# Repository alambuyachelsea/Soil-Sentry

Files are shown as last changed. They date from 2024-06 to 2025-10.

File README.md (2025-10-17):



## Table of contents
- [Author](#author)
- [Project Overview](#project-overview)
- [Estimated Time](#estimated-time)
- [Project Objective](#project-objective)
- [Bill of Materials](#bill-of-materials)
- [Computer Setup](#computer-setup)
  - [IDE](#ide)
  - [Raspberry Pi Pico W Setup](#raspberry-pi-pico-w-setup)
  - [Wiring](#wiring)
- [Platform for Data Transmission](#platform-for-data-transmission)
- [The Code](#the-code)
  - [Controller Code](#controller-code)
  - [Server Code](#server-code)
- [Final Look](#final-look)

## Author
By Alambuya Chelsea

## Project Overview
The soil sentry is a small scale irrigation system which allows a user to connect multiple plants with various water consumption needs, monitor their water levels and supply water them when needed in addition to monitoring the water reservoir levels. 

## Estimated Time
- Setting up the whole project with the IDE and getting everything connected takes about 5 hours with 2 hours of active setup and about 3 hours for designing a 3D printing the reservoir mount where ultrasonic sensor will rest. The container I chose for the reservoir was relatively small so this the printing did not take much time, see the picture below
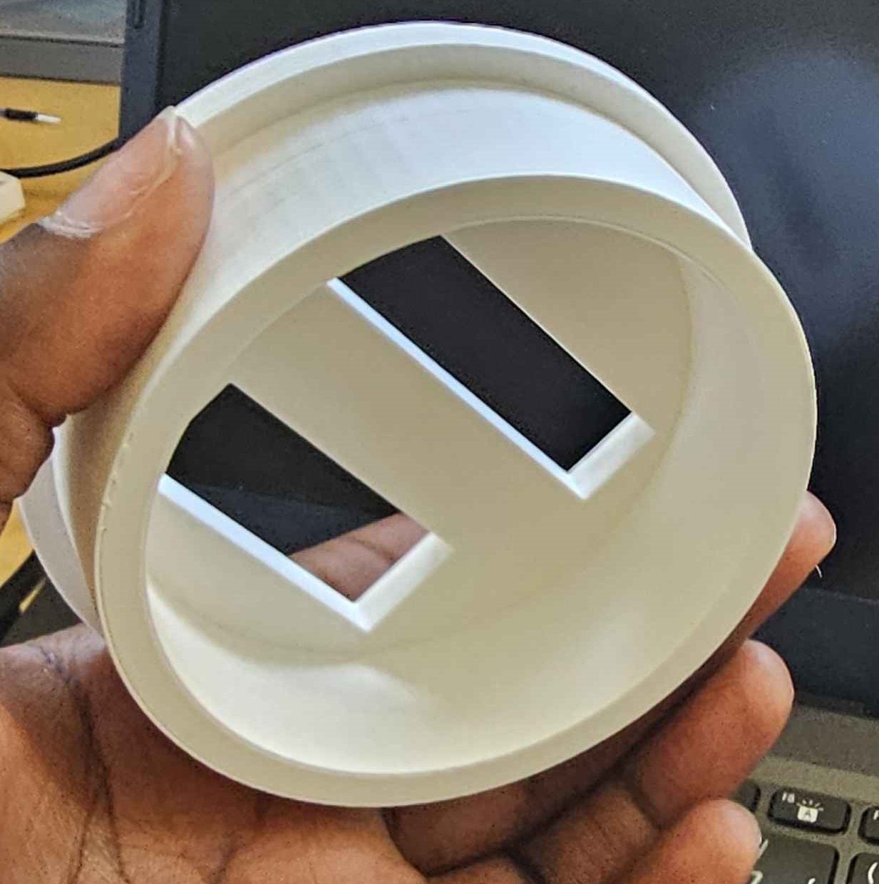
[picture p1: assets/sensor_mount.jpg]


## Project Objective
Many at home watering solutins exist but are limited to just soil moisture levels and water supply. These solutions are sufficient for plants that have the same water consumption needs but to an owner of various plant types like succulents, herbs and flowering plants this can lead to over or under watering plants by trying to calibrate a single water supply to them.
With the soil sentry, a user can create differnt plant profiles where each plant's water consumption needs will determine how offen it recieves water from the supply. Additionally, the water reservoir is monitored which allows the user to know when re-fill it.
By monitoring the data, users can have a better idea of their plant needs, reduce water waste by ensuring the plants are only watered when they need it.

## Bill of Materials
These items can be purchased online at stores that sells electronic components, single board computers, modules, sensors etc. Reliable options are [The pi hut](thepihut.com), [electrokit](electrokit.com), [amazon.se](amazon.se) and any non electronic components can be found at a hardware store.
|Image|Component|Price (SEK)|Purpose|
|---|---|---|-----|
|Raspberry Pi Pico W |Raspberry Pi Pico W| 89| Reads the sensor data and transmits it to the server|
|Soil Moisture Sensor |Capacitive Soil Moisture Sensor V2.0 *| 44| To measure the soil moisture level |
|Submersible waterpump 3V |Submersible waterpump 3V *| 45| To pump the water from the reservoir to the plants|
|5V Relay Module|5V Relay Module *| 60|Handles switching operations between the 3V pump and a separate 5V control signal|
|9V Battery|9V Battery|60|Power Supply for the water  pumps|
|Battery cord|Battery cord|20|Connects battery to power supply module|
|Breadboard Power Supply Module|Breadboard Power Supply Module|60|Power Supply to the breadboard for the water  pumps|
|HC-SR04 Ultrasonic Range Sensor|HC-SR04 Ultrasonic Range Sensor| 23| To measure the reservoir level|
|Male-Male Jumper Wires|Male-Male Jumper Wires| 100| To connect components to the Pico|
|Female-Male Jumper Wires|Female-Male Jumper Wires| 100| To connect components to the Pico|
|Female-Female Jumper Wires|Female-Female Jumper Wires| 100| To connect components to the Pico|
|Silicon Water Pipe|Silicon Water Pipe| 45| To transport water to the plant|
|2 Core Electric Cable|2 Core Electric Cable| 121| To extend the length of jumper wires|
|Soldering Iron Kit|Soldering Iron Kit| 500| To join 2 wires|
|Solder Wire|Solder Wire| 100| To join 2 wires|
|Desoldering Wick|Desoldering Wick| 100| To erase the makes you made (with the soldering, not in real life)|
|Electric Tape|Electric Tape| 60| To seal soldered wires that will be placed in water|
|Heat Shrink|Heat Shrink| 90| To seal soldered wires that will be placed in water|

  * Get one per plant you intend to monitor

## Computer Setup
### IDE
I developed this on a computer running windows 11. I decided to use Thonny for the microcontroller code because it is specifically designed for beginners in MicroPython programming, offering an intuitive interface, easy debugging tools for microcontroller projects. Installation instruction can be found on the [Thonny website](https://thonny.org/). For the server side code I used VS Code which you can download and install on the [Visual Studio Code website](https://code.visualstudio.com/download)

### Raspberry Pi Pico W setup
To set up the pico first download the latest version of Raspberry Pi Pico W firmware [here](https://rpf.io/pico-w-firmware), once downloaded connect the pico to your computer while holding down the bootsel button. A file manager should open with the raspberry pi pico w as the connected device, copy the firmware file to the device and the file manager will close. Open the Thonny editor and on the navigation bar, select Tools > Options > Interpreter and choose the MicroPython interpreter for Raspberry Pi Pico.

### Wiring
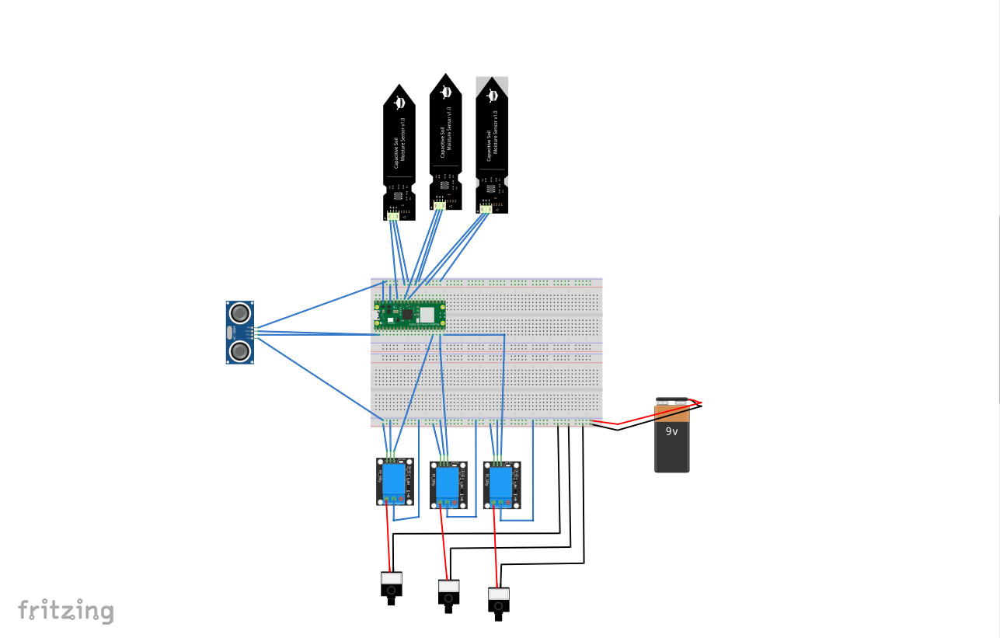
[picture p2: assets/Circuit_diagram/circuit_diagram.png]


- Breadboard - I connected 2 boards to reduce crowding but it's possible to have everything on one.

- Raspberry Pi Pico W - place the Pico over the center of the breadboard with the pins straddling the center divide. Connect the pico's GND to the (-) line on the right side of the breadboard and the 3V3 output to the (+) line on the on the right side of the breadboard. See the attached pico w pinout for guidance. 
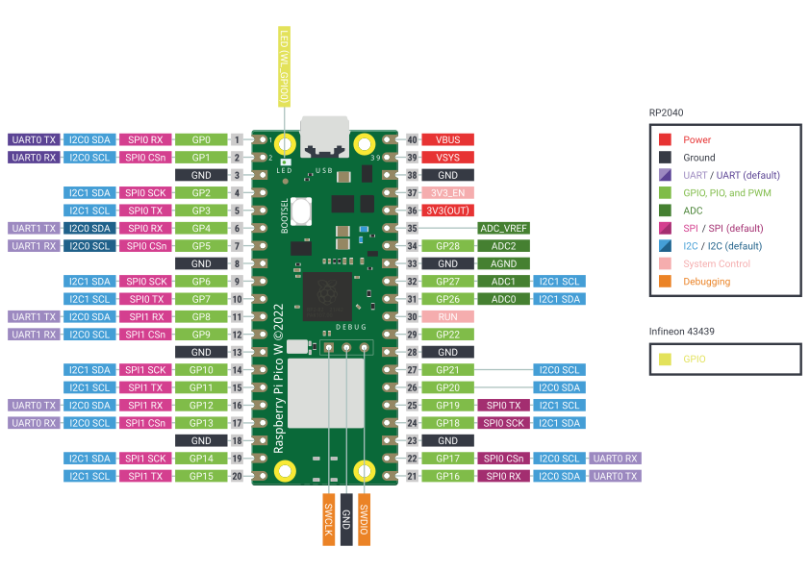
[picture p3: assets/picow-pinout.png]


- Power Supply module and 9V Battery - Connect the battery to the power supply module using the battery cord. Connect the power supply's GND pin to the left side (-) line and the 5V pin to the left side (+) line, turn on the power supply by pressing the power button.

- Soil moisture sensors - For my set up, I used analog sensors so I was limited to 3 analog to digital converter (ADC) pins on the pico i.e. GP26, GP27 and GP28. This will be placed in the soil to measure the moisture content. Connect the sensor's vcc to the (+) line on the bread board, the GND to the (-) line on the breadboard and the analog output to one of the ADC pins. Since soil sensors are different you may have to calibrate them according to your environment. Follow these steps to calibrate them;

  - Take readings in open air, very dry soil, dry soil, lightly watered soil, heavily watered soil and 100% water. 
  - Take about 100 readings for each  and find the highest and lowest values
  - Create a scale of 0 - 5 where 0 is open air and 5 is 100% water.

- Ultra sonic sensor - This should rest on top of the water reservoir. For this project, I designed a 3D mount to set on top of the reservoir. Connect the sensor's GND to any (-)line on the breadboard and the vcc to any (+) line on the breadboard. Connect the trig pin to GPIO 0 and connect the echo pin to GPIO 1.
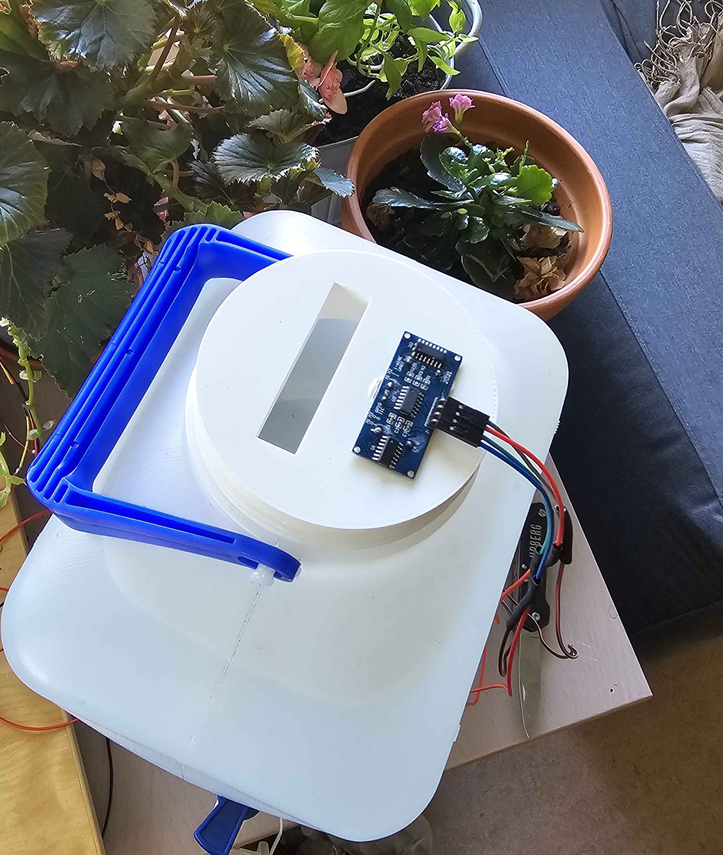
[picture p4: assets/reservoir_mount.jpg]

Calibrating the ultra sonic sensor is similar to the soil moisture sensors;
  - Set up the sensor above the reservoir and take readings when the reservoir is empty, and slowly increase the water level taking several readings as you go.
  - Create a percentage scale after getting the reading at multiple levels.

- Water Pump and 5V relay module - Connect the water pump's gnd to the left side (-) line on the breadboard and the the pump's (+) line to the relays normally open(NO) terminal. Then connect the relay's (-) and (+) pins to the GND and the (+) line on the left side of the breadboard. Connect the relays control input pin to any available GPIO pin.

### Platform for Data Transimission
- For the project, I decided to send the sensor data via a json data file sent over HTTP. I set up a server on my laptop to listen for data transmitted by the pico inorder to process it. 
- When the pico connects to the same network as the server, the sensor data is read and transmitted to the server as a POST request and stored as a variable. 
- When the dashboard is requested for from a browser, the server servers the index.html file (styled with css) and JavaScript method requests for the data to be displayed. 
- At this point, the data has been recieved by the server and stored in a variable so this information is sent. I decided to create a custom dashboard as I felt the available options were too restricting in how the data could be visualized and additionally I could style it to my preference.

### The Code
#### Controller Code
The code is fairly straight forward. In controller_code folder is the code to be uploaded to the Raspberry Pi Pico W and works as follows,
  - plant_profile.py: This class allows different plant types to be created with specific water needs, a soil sensor pin and a water pump pin.
  - water_pump.py: This allows the water to be turned on and off when a plant requires water
  - Soil_sensor.py: This takes the soil moisture level and converts it according to the scale created during the sensor calibration
  - ultrasonic_sensor.py: This transimits a sonic pulse, waits for an encho and uses the time difference to determine how far the water is from the sensor, this is then converted to an approximate percentage of remaining water in the reservoir.
  - main.py: This is where different plant profiles are created with their respective soil sensors and water pump pins. The ultra sonic sensor is also initialized with the trigger and echo pins. The program then periodically reads data from the various sensors and transmits it to the server via an HTTP POST request. After the data is transmitted, the reservoir level is checked to make sure there's enough enough water to water  the plants, if there is, all the plants' current water levels are checked to see if they fall below their water needs. If the water level is below their needs, then it's associated pump is turned on for 10 seconds which provides sufficient water to increase it's current water level and then turned off. After one hour, the process is repeated.

#### Server code
This Python script sets up a system to manage sensor data through both an HTTP server and a WebSocket server. The HTTP server, built using `BaseHTTPRequestHandler` and `HTTPServer`, handles GET requests to serve static files like `index.html`, `styles.css`, and `script.js`, as well as JSON data for endpoints such as `/plants` and `/ultrasonic_reading`. It also handles POST requests to receive sensor data at the `/receive_data` endpoint, storing this data in a global dictionary `sensor_data`. When new sensor data is posted, it is also sent to all connected WebSocket clients using asynchronous communication.

The WebSocket server, created with the `websockets` library, manages real-time communication with clients. It handles incoming WebSocket connections and responds to requests for sensor data. A function `send_data_to_clients` is used to broadcast updated sensor data to all connected WebSocket clients. Both servers are run concurrently: the HTTP server in a separate thread and the WebSocket server in the main thread, allowing the system to handle HTTP requests and WebSocket communication simultaneously. This setup facilitates a dashboard webpage where clients can receive dynamic updates of sensor data in real-time.

## Data Visualization
The dasboard can be deívided into 3 main parts
- The Reservoir. This shows the reservoirs approximate level after readings are taken and converted to a percentage.
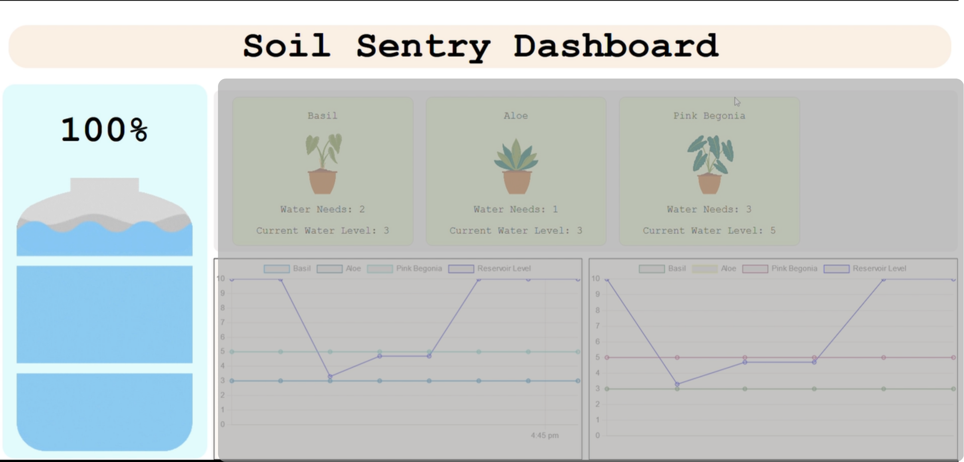
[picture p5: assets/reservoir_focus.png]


- Plant section. Here the user can view all the plants currently being monitored, their name, current water level (which is updated every hour) and water needs
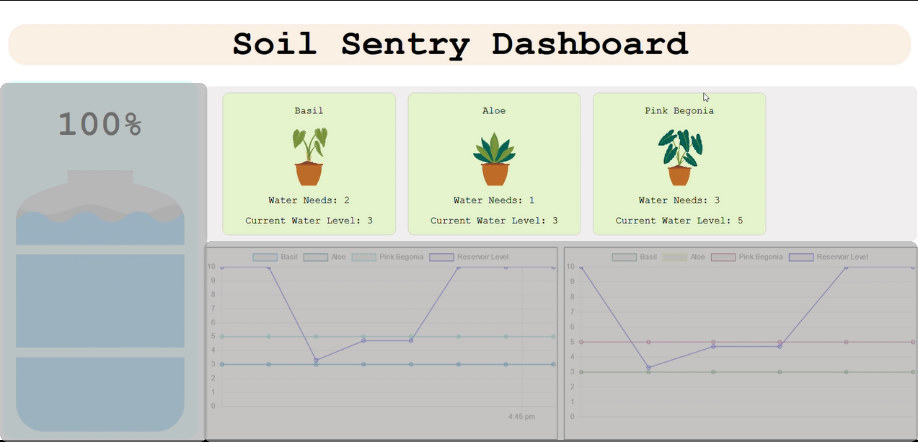
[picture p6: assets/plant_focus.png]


- Graph section. This further split into:
  - Hourly section. This shows the plants current water level as the rservoir level and this is recorded every hour of the day.
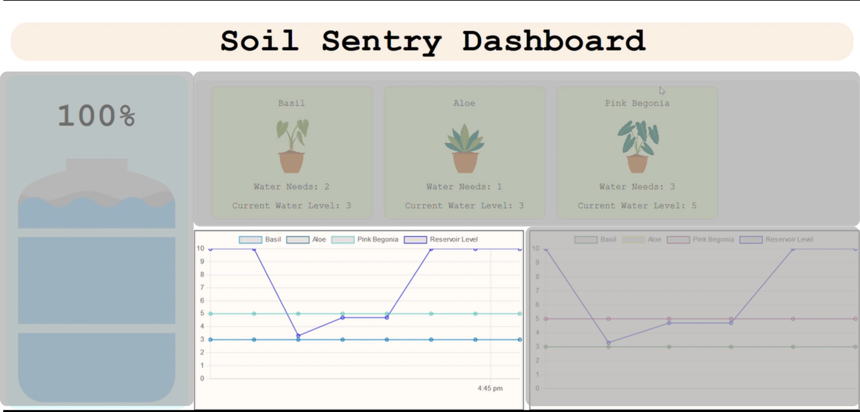
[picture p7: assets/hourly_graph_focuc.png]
  

  - Weekly section. This shows that plants average water level for the last 24 hours
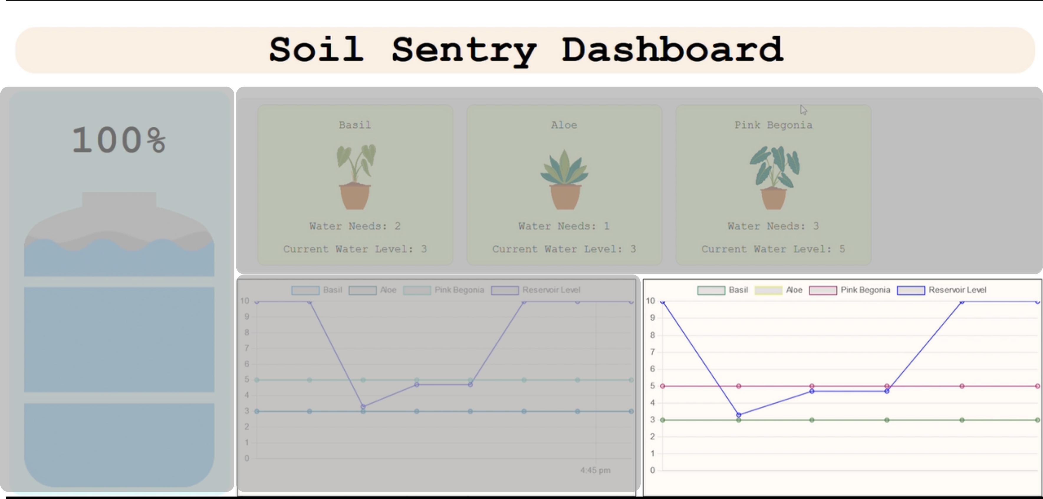
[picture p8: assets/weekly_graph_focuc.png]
  

## Final look
Over all, the roject turned out as I origianlly designed but throught out the process I realized I was limited to only 3 three ADC pins on the pico so if i wanted to add more plants I'd have to purchase an additional digital soils sensor. It was also quite difficult to calibrate the soil sensors as they were quite immprecise and had verry different ranges.

The final dashboard
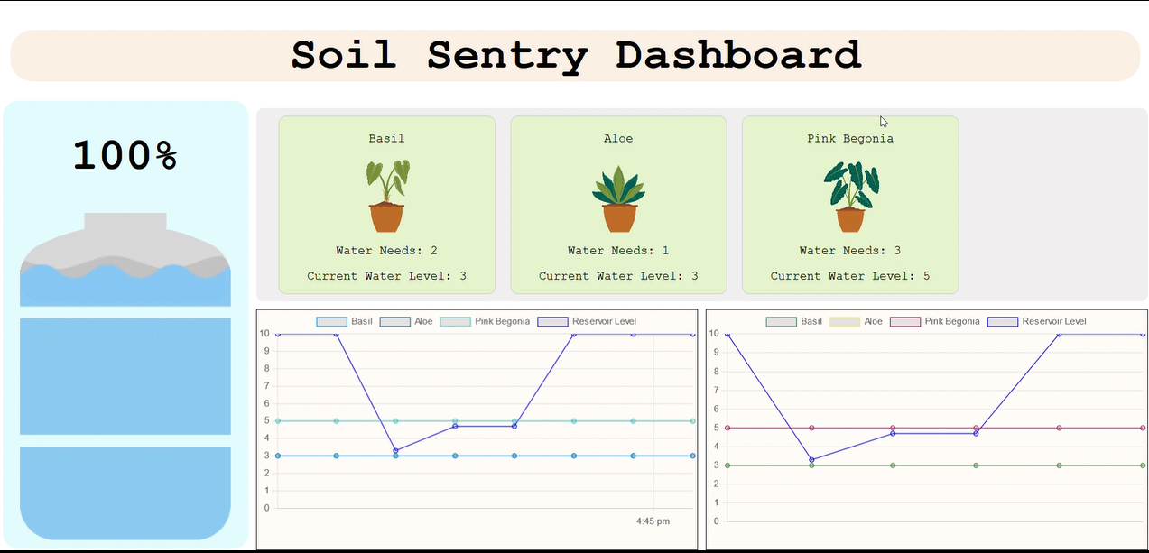
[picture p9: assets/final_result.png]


Plant window with multiple plants



Final Setup shot 1
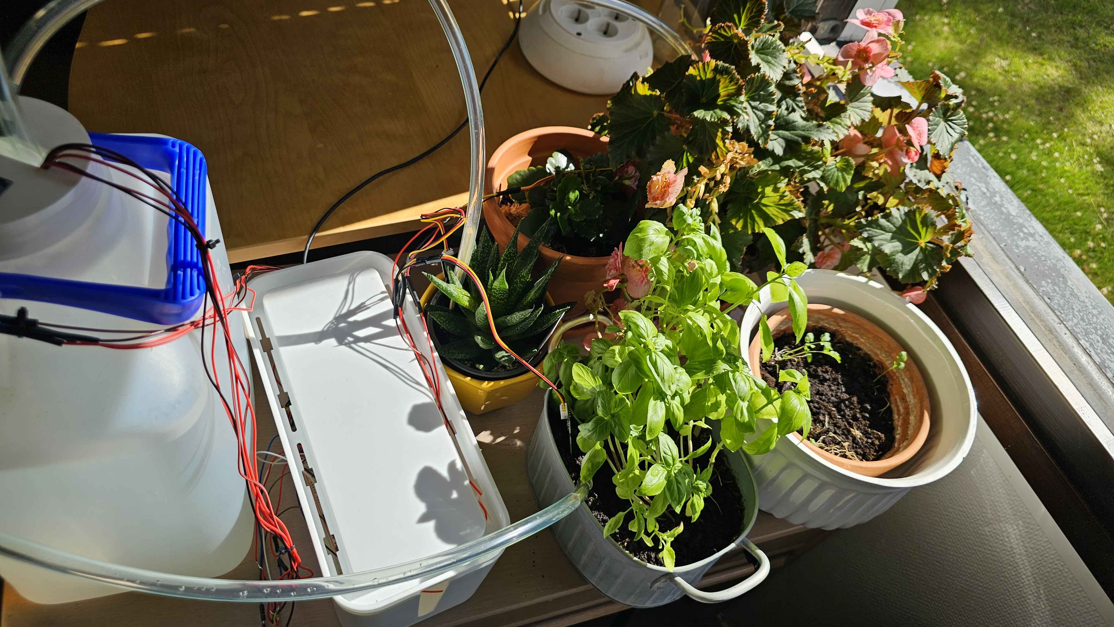
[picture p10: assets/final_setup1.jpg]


Final setup shot 2
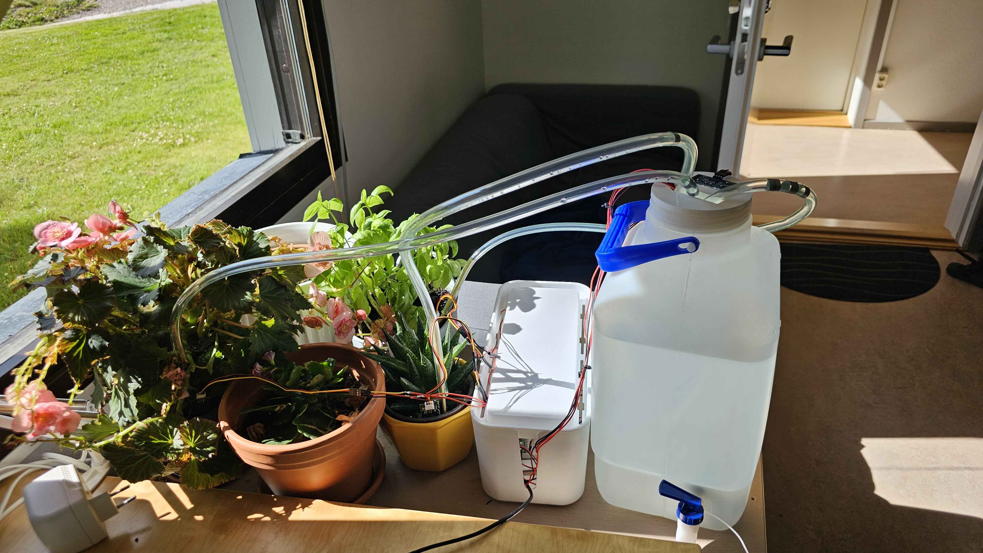
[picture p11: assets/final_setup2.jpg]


## Youtube Video 
Check out [this](https://youtu.be/vv5wq6jMT6I) youtube video to see the dashboard in action.

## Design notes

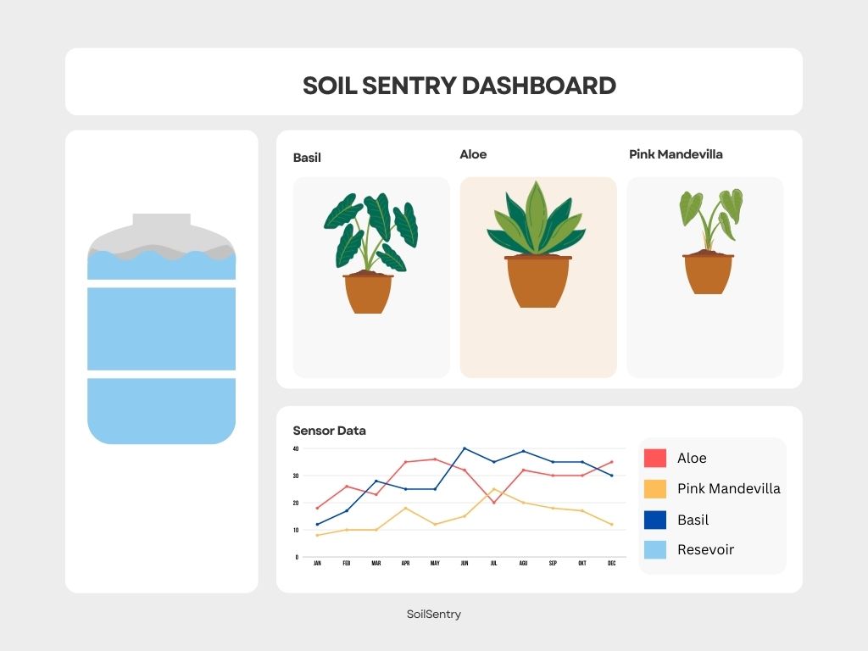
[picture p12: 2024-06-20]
webpage/Orange Cute Website Analytics Report Statistical Graph.jpg

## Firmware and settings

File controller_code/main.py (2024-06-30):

import network
import time
import urequests as requests
import json
from ultrasonic_sensor import UltrasonicSensor
from plant_profile import PlantProfile

# Wi-Fi Credentials
ssid = "netwrok name"
password = 'network password'

# Connect to Wi-Fi
wlan = network.WLAN(network.STA_IF)
wlan.active(True)
wlan.connect(ssid, password)

# Wait until connected
while not wlan.isconnected():
    pass

print('Connected to Wi-Fi')
print('IP Address:', wlan.ifconfig()[0])

# HTTP endpoint (replace with your server URL)
# Change URL where the server receives data
server_url = 'http://serverURL:serverPortNumber/receive_data'

# Plant profiles with sensor pins
plants = [  # Change according to the number and needs of the plants
    PlantProfile(name="Basil", water_needs=2, pump_pin=14,
                 sensor_pin=28, img_source='https://i.imgur.com/w8xuEfx.gif'),
    PlantProfile(name="Aloe", water_needs=1, pump_pin=13,
                 sensor_pin=27, img_source='https://i.imgur.com/e9EikGU.gif'),
    PlantProfile(name="Pink Begonia", water_needs=3, pump_pin=15,
                 sensor_pin=26, img_source='https://i.imgur.com/phBFJkd.gif'),
]

# Initialize ultrasonic sensor
ultrasonic_sensor = UltrasonicSensor(trigger_pin_num=0, echo_pin_num=1)


# Function to read soil moisture and ultrasonic sensor
def water_plants():
    if get_reservoir_level() > 20:

        for plant in plants:
            print(plant.get_name(), plant.get_current_water_level(),
                  plant.get_water_needs())

            if plant.get_current_water_level() < plant.get_water_needs():
                plant.water_self()


def get_reservoir_level():

    distance = ultrasonic_sensor.read_distance()
    percentage = ultrasonic_sensor.convert_sonic_reading_to_percentage(
        distance)
    return percentage


# Function to read sensor data from all plants and ultrasonic sensor
def read_sensors():
    readings = {}

    # Read soil moisture sensors
    plant_data = [
        {
            "name": plant.get_name(),
            "water_needs": plant.get_water_needs(),
            "current_water_level": plant.get_current_water_level(),
            "img_source": plant.get_img_source()
        }
        for plant in plants
    ]
    readings["plants"] = plant_data

    try:  # Read ultrasonic sensor
        percentage = get_reservoir_level()
        readings["level"] = percentage

    except Exception as e:
        print("Error reading ultrasonic sensor:", e)
        readings["level"] = None

    return readings


# Function to send sensor data via HTTP POST
def send_sensor_data():
    data = read_sensors()

    # Prepare JSON message
    json_data = json.dumps(data)

    # Send HTTP POST request
    try:

        headers = {'Content-Type': 'application/json'}
        response = requests.post(server_url, data=json_data, headers=headers)
        print('HTTP POST Status:', response.status_code)
        response.close()

    except Exception as e:
        print("Error sending HTTP POST request:", e)


# Send sensor data periodically
while True:
    send_sensor_data()

    # Water plants if reservoir level is above 20%
    water_plants()

    time.sleep(3600)  # Delay between readings in seconds

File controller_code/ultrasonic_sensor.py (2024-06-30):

import machine
import utime


class UltrasonicSensor:

    def __init__(self, trigger_pin_num, echo_pin_num):
        self.trigger_pin = machine.Pin(trigger_pin_num, machine.Pin.OUT)
        self.echo_pin = machine.Pin(echo_pin_num, machine.Pin.IN)

    def read_distance(self):

        # Send a 10us pulse to trigger the sensor
        self.trigger_pin.value(1)
        utime.sleep_us(10)
        self.trigger_pin.value(0)

        # Wait for the echo pin to go high
        while self.echo_pin.value() == 0:
            pulse_start = utime.ticks_us()

        # Wait for the echo pin to go low again
        while self.echo_pin.value() == 1:
            pulse_end = utime.ticks_us()

        # Calculate the duration of the pulse
        pulse_duration = utime.ticks_diff(pulse_end, pulse_start)
        # Speed of sound is approximately 343 meters per second
        # Divide by 2 to account for round trip
        distance = (pulse_duration * 34300) / 2

        # Round the distance to 4 decimal places
        distance_rounded = round(distance, 4)

        return distance_rounded

    def convert_sonic_reading_to_percentage(self, reading):

        # Define the scale thresholds with corresponding percentage values
        thresholds = [
            (3.6015e+07, 0),      # empty reservoir (0%)
            (3.41628e+07, 6),
            (3.195045e+07, 13),
            (2.92922e+07, 20),
            (2.74057e+07, 27),
            (2.46617e+07, 33),
            (2.31182e+07, 40),
            (2.148895e+07, 47),
            (1.97225e+07, 53),
            (1.733865e+07, 60),
            (1.534925e+07, 67),
            (1.31369e+07, 73),
            (1.15248e+07, 80),
            (9844100.0, 86),
            (7443100.0, 93),
            (4750550.0, 100),     # full reservoir (100%)
        ]

        # Determine the percentage value based on thresholds
        for threshold, percentage in thresholds:
            if reading >= threshold:
                return percentage
        return 100.0  # Default to 100% if below the lowest threshold

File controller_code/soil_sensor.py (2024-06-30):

from machine import ADC


class SoilSensor:
    def __init__(self, pin_number):
        self.adc = ADC(pin_number)

    def read_moisture_level(self):
        return self.adc.read_u16()  # Returns a value between 0 and 65535

    def measure_current_water_level(self):
        reading = self.read_moisture_level()
        level = self.convert_soil_moisture_to_scale(reading)
        return level

    def convert_soil_moisture_to_scale(self, reading):
        thresholds = [
            (24293, 0),  # Air in a dry room
            (24093, 1),  # Extremely dry soil
            (21060, 2),  # Dry soil
            (17684, 3),  # lightly watered soil
            (15991, 4),  # heavily watered soil
            (13713, 5)   # 100% water
        ]

        for threshold, scale_value in thresholds:
            if reading >= threshold:
                return scale_value
        return 5  # Default to 5 if below the lowest threshold

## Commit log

2024-06-20 initial pico code
2024-06-20 water pump class
2024-06-20 sensor classes
2024-06-26 ultra sonic sonic sensor class
2024-06-27 switched measurement to soil sensor class
2024-06-30 circuit diagram
    [Circuit_diagram.kicad_pcb, Circuit_diagram.kicad_sch, Untitled Sketch.fzz]
2024-07-01 folder oragnization
    [Circuit_diagram.kicad_pcb, Circuit_diagram.kicad_sch, Untitled Sketch.fzz]
2024-07-04 sensor mount image added
